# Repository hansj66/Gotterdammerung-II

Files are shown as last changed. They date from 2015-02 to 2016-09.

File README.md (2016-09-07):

# Götterdämmerung II 3D-printer

GD2

This is the second iteration of the Götterdämmerung. The following improvements have been made:
- Core XY'ish layout. 
- Dual 24V power. 
- Improved Z stage.
- Geared stepper extruder, using M2 type filament drive.
- Designed for using cable towing chains.

Suggestions for selecting necessary third party stuff for building a complete printer

- Use 24 V power. This will enable you to run the steppers faster and use thinner wires. Also use a separate power supply for the heated bed (driven via a solid state relay)
- Buy a decent hot end. E3D with a 0.8 mm nozzle (or bigger) works fine with this printer.
- Use glass fiber reinforced timing belts.
- Use low impedance steppers.

Rumba board (supports 24V) with DRV8825, configured for 1/16 microstepping works fine with this printer. 

This is a working design, but it is still in development. 

The printer frame is made of 40x40 mm aluminium extrusions and it is extremely rigid. All idlers use ball bearings and 
the combination of 12mm steel axis and linear bearings ensures a stable platform.
The design scales in X/Y/Z without changes to any printed parts.

Build instructions (work in progress)  can be found on the wiki pages: https://github.com/hansj66/Gotterdammerung-II/wiki

Other stuff that has been printed on this printer:

Model from Bold machines. Scaled to approximately 25x20x14 cm in size.
Margo's Dog

Dante bust (29 x 30 x 26 cm). 13 hours print with 0.8mm nozzle, 0.3mm layer height

Dante

Strandbeest inspired robots. Theo Jansen linkage, but with parameters based on output from my own genetic algorithm). 80+ hours printing time.

City Beest

CityBeest mk II

This design is made available under the under the Creative Commons Attribution-ShareAlike CC BY-NC-SA license (https://creativecommons.org/licenses/by-nc-sa/4.0/)



Hans Jørgen Grimstad
www.TimeExpander.com

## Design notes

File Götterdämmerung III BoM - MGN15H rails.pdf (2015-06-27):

Item # | Count | Dimension | Description
1 | 9 | (m) 40x40 | aluminium profile
2 | 24 | 40 x 40 | aluminium angle brackets
3 | 50 | M8 | T-nuts
4 | 40 | M8 | 15 mm hex head bolt
5 | 10 | M8 | 25 mm hex head bolt
6 | 2 | | 24V Power Supply (360W+ for heatbed PS)
7 | 1 | | Rumba board
8 | 4 | | DRV8825 + heatsinks
9 | 1 | | Ramps 1.4 smart controller (Display, SD, Encoder)
10 | 1 | | Geared Nema 17
11 | 3 | | Nema 17 1,8 A
12 | 4 | 500 mm | 8mm Lead Screw with nut
13 | 2 | 500 mm | 12 MM Steel rods
14 | 2 | 500 mm | MGN15H Linear rails (25x25mm M3 hole separation on carriage)
15 | 1 | 600 mm | MGN15H Linear rails (25x25mm M3 hole separation on carriage)
16 | 16 | OD: 22 ID 8 H 7 | Ball bearings
17 | 20 | M8 | washer
18 | 4 | M8 | hex nut
19 | 14 | ID: 8: OD 30 | M8 washer
20 | 4 | ID: 8 mm | GT2 pulleys
21 | 3 | ID: 5 mm | GT2 pulleys
22 | 2 | LM12UU | Linear bearings
23 | 4 | m | Open GT2 belt
24 | 1 | 1524 mm | Closed GT2 belt
25 | 1 | 5x8 | Flexible shaft coupling
26 | 2 | 500 mm (10 x 1 | CNC Cable Carrier Drag Chain
27 | 1 | E3D HotEnd | (Or other J-head equivalent)
28 | 1 | 8 x 25 mm spring
29 | 2 | 200x300 | Heatbed
30 | 2 | 200x300 | Cork insulation

31 | 1 | 100k ? | Thermistor for heatbed
32 | 2 | 68x145x200mm | Enclosure
33 | 1 | Ø 25 mm | Rod for spool holder
34 | 20 | (m) | Wiring. Different colours
35 | 3 | | End stops + cables
36 | 20 | 5mm | M3 screws
37 | 50 | 20 mm | M3 screws
38 | 1 | m | 6mm carbon tube/rod
39 | 1 | | Solid State DC Relay (SSR-25DD or equivalent)
40 | 1 | | Build plate, MDF (16 x 400 x 440 mm)
41 | 1 | | Aluminium sheet, 1 x 400 x 440 mm)
42 | 1 | | Glass plate ( 3 x 400 x 440 mm)
43 | | | Printed parts
44 | 1 | | http://www.thingiverse.com/thing:494430

Subject to change as improvements are made

All non-printed parts for the initial version were sourced from eBay or AliExpress for approx $1100

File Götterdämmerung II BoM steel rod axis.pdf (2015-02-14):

Item # | Count | Dimension | Description
1 | 9 | (m) 40x40 | aluminium profile
2 | 24 | 40 x 40 | aluminium angle brackets
3 | 50 | M8 | T-nuts
4 | 40 | M8 | 15 mm hex head bolt
5 | 10 | M8 | 25 mm hex head bolt
6 | 2 | | 24V Power Supply (360W+ for heatbed PS)
7 | 1 | | Rumba board
8 | 4 | | DRV8825 + heatsinks
9 | 1 | | Ramps 1.4 smart controller (Display, SD, Encoder)
10 | 1 | | Geared Nema 17
11 | 3 | | Nema 17 1,8 A
12 | 2 | (m) | M8 Z screw
13 | 6 | 500 mm | 12 MM Steel rods
14 | 16 | OD: 22 ID 8 H 7 | Ball bearings
15 | 20 | M8 | washer
16 | 4 | M8 | hex nut
17 | 14 | ID: 8: OD 30 | M8 washer
18 | 4 | ID: 8 mm | GT2 pulleys
19 | 3 | ID: 5 mm | GT2 pulleys
20 | 6 | LM12UU | Linear bearings
21 | 4 | m | Open GT2 belt
22 | 1 | 1524 mm | Closed GT2 belt
23 | 1 | 5x8 | Flexible shaft coupling
24 | 2 | 500 mm (10 x 1 | CNC Cable Carrier Drag Chain
25 | 1 | E3D HotEnd | (Or other J-head equivalent)
26 | 1 | 8 x 25 mm spring
27 | 2 | 200x300 | Heatbed
28 | 2 | 200x300 | Cork insulation
29 | 1 | 100k ? | Thermistor for heatbed
30 | 2 | 68x145x200mm | Enclosure

31 | 1 | Ø 25 mm | Rod for spool holder
32 | 20 | (m) | Wiring. Different colours
33 | 3 | | End stops + cables
34 | 20 | 5mm | M3 screws
35 | 50 | 20 mm | M3 screws
36 | 1 | m | 6mm carbon tube/rod
37 | 1 | | Solid State DC Relay (SSR-25DD or equivalent)
38 | 1 | | Build plate, MDF (16 x 400 x 440 mm)
39 | 1 | | Aluminium sheet, 1 x 400 x 440 mm)
40 | 1 | | Glass plate ( 3 x 400 x 440 mm)
41 | | | Printed parts
42 | 1 | | http://www.thingiverse.com/thing:494430

Subject to change as improvements are made

All non-printed parts for the initial version were sourced from eBay or AliExpress for approx $1000

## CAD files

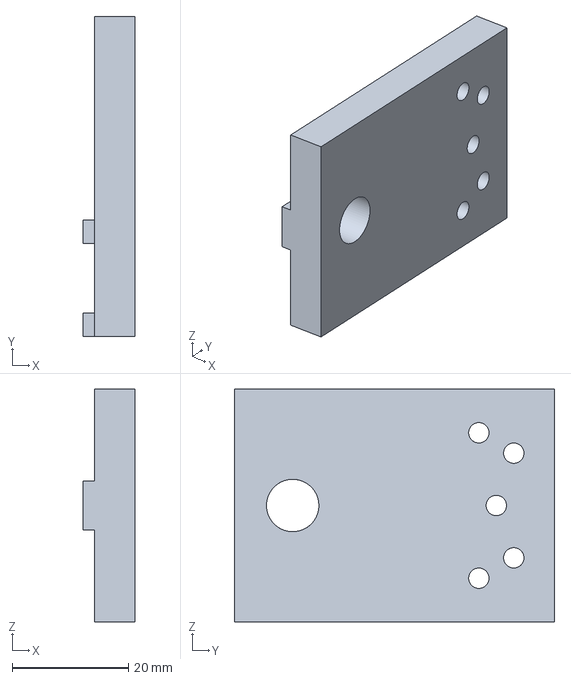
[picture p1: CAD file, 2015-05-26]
printed_parts/beta/IGES/Generic_Power_Mount_Small.igs
9.00 x 55.0 x 40.0 mm

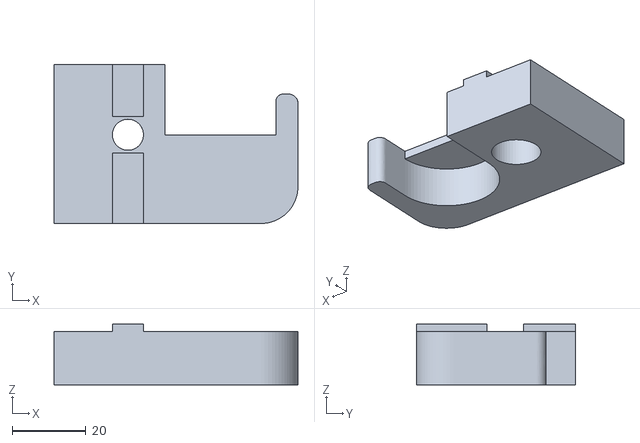
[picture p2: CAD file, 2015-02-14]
printed_parts/beta/STL/FilamentRodHolder_L.stl
66.0 x 43.0 x 16.5

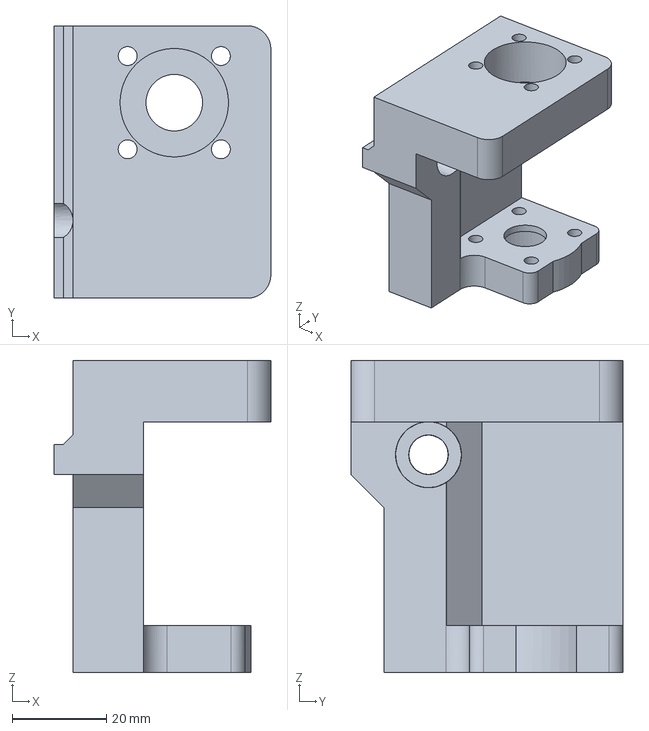
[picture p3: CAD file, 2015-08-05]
printed_parts/production/IGES/z-stepper-mount-geared.igs
46.0 x 57.8 x 66.2 mm

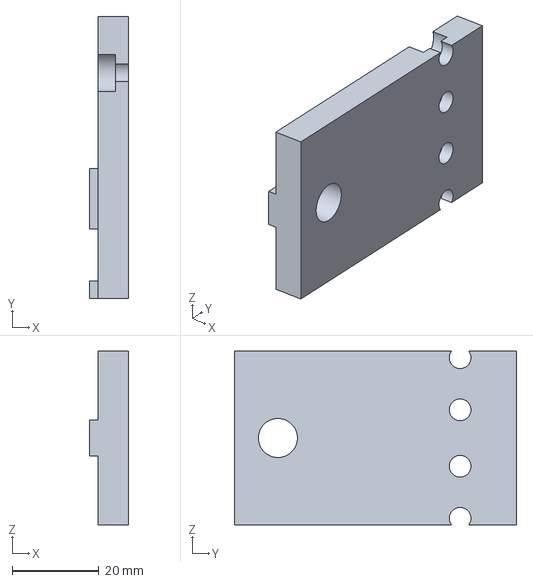
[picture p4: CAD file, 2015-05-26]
printed_parts/beta/IGES/Generic_Power_Mount_Big.igs
9.00 x 65.0 x 40.0 mm

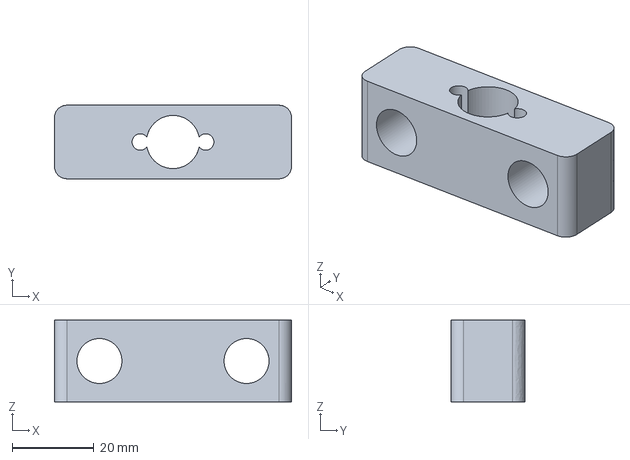
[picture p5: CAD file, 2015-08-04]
printed_parts/production/IGES/z-adjustment-T8.igs
58.0 x 18.0 x 20.0 mm

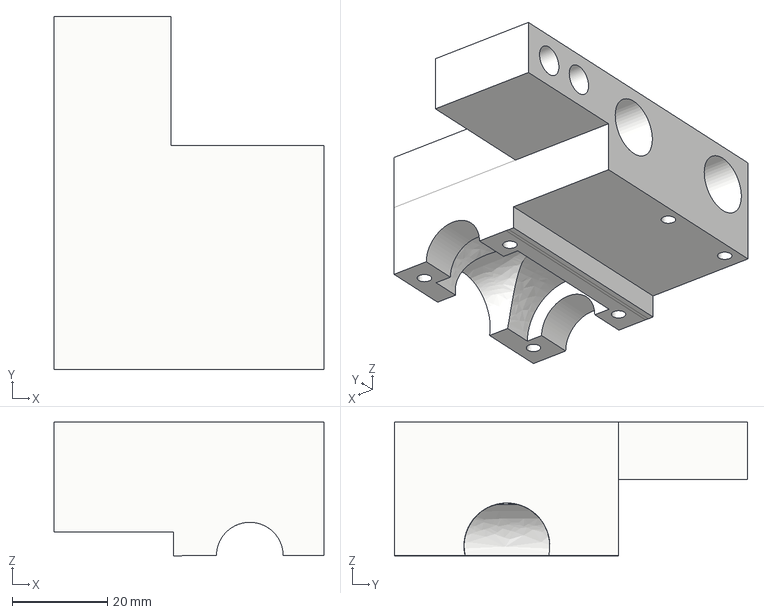
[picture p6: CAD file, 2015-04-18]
printed_parts/beta/IGES/Y_Carriage_Left_2.igs
56.5 x 74.0 x 28.0 mm

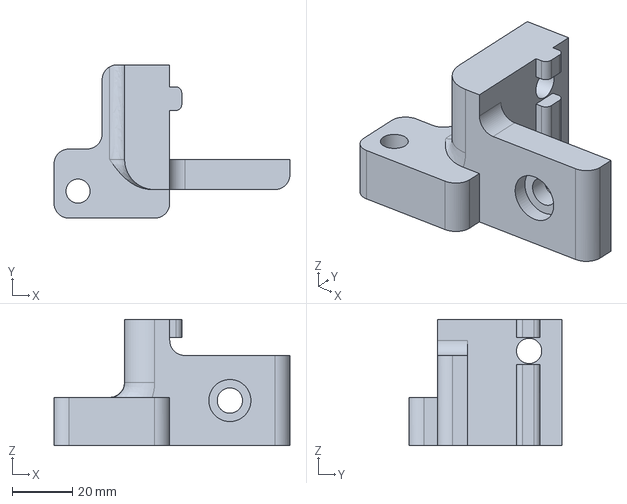
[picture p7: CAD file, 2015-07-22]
printed_parts/production/IGES/XY_Idler_Left.igs
78.5 x 51.0 x 42.0 mm

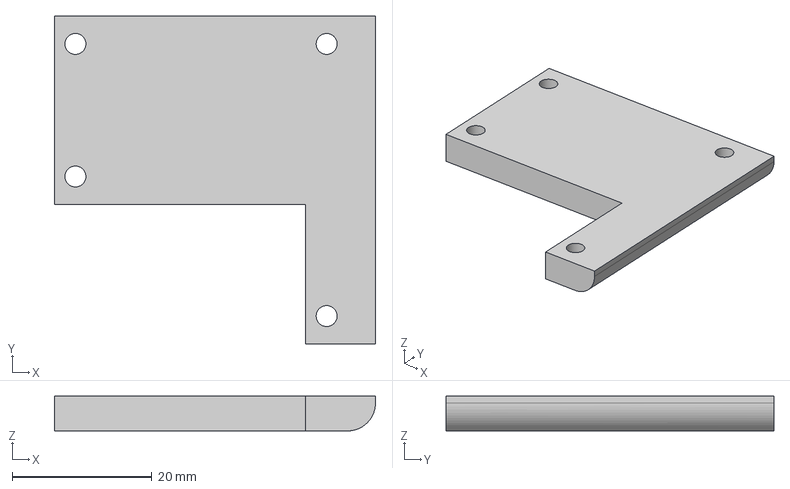
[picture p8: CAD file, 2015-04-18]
printed_parts/beta/IGES/Y_Carriage_Right_4.igs
46.0 x 47.0 x 5.00 mm

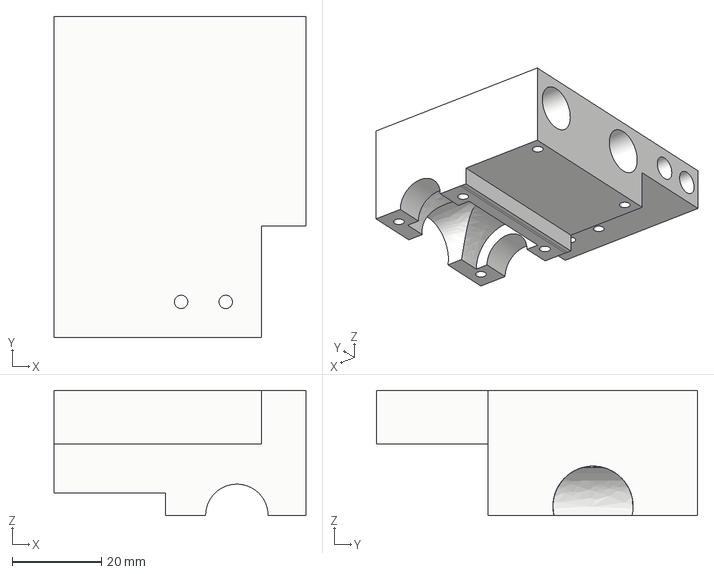
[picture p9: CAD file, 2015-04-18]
printed_parts/beta/IGES/Y_Carriage_Right_2.igs
56.5 x 72.0 x 28.0 mm

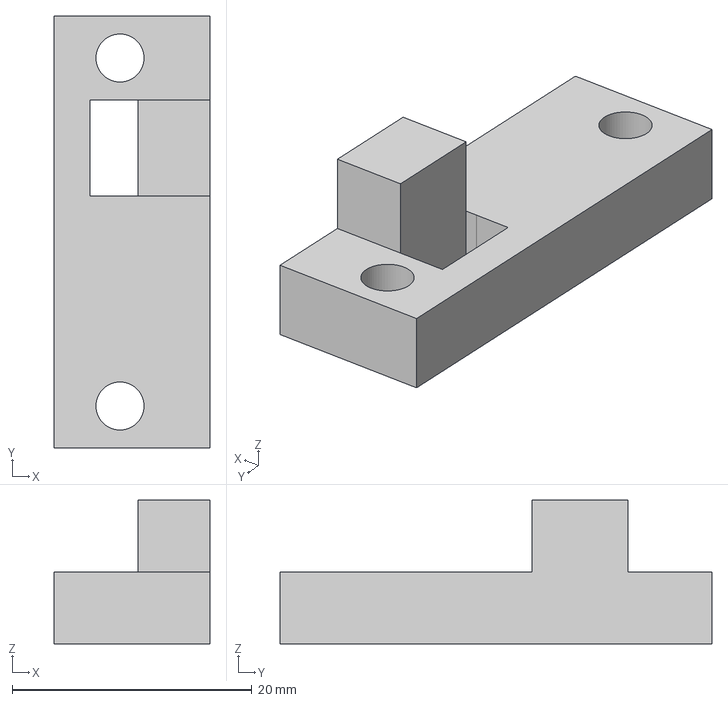
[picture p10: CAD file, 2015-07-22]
printed_parts/production/IGES/Clamp1.igs
13.0 x 36.0 x 12.0 mm

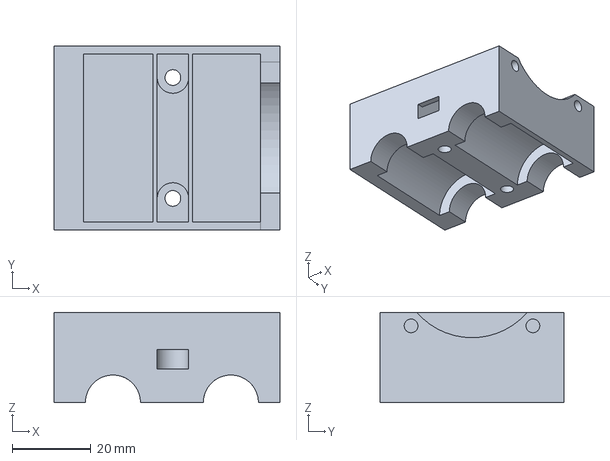
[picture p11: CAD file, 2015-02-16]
printed_parts/beta/IGES/X_Carriage_7.igs
57.5 x 46.8 x 22.9 mm

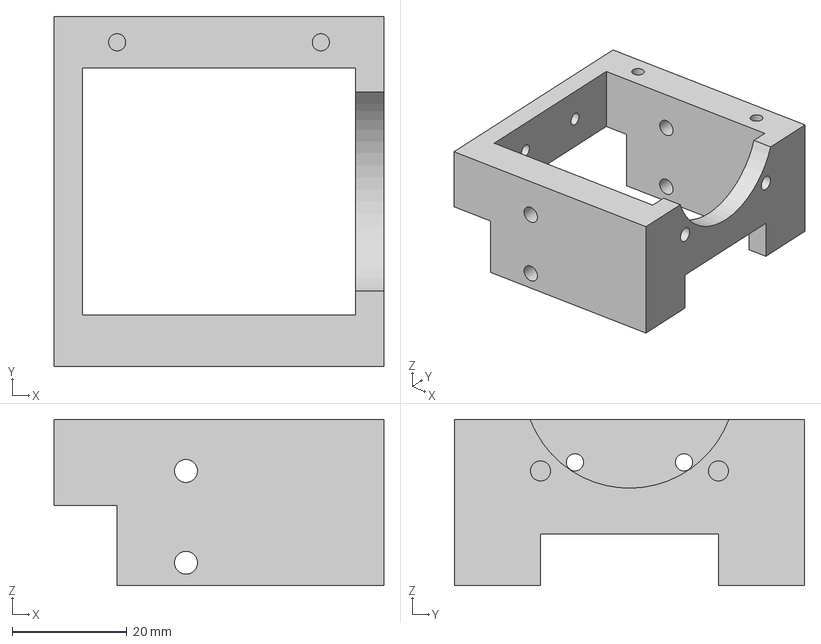
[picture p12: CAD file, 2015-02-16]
printed_parts/beta/IGES/X_Carriage_2.igs
57.5 x 61.0 x 29.0 mm

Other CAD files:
printed_parts/production/STL/FilamentRodHolder_R.stl
printed_parts/beta/STL/FilamentRodHolder_R.stl
printed_parts/production/IGES/XY_Idler_Right.igs
printed_parts/production/IGES/Clamp3.igs
printed_parts/production/IGES/Clamp2.igs
printed_parts/beta/IGES/ATX_Power_Mount_1.igs
printed_parts/beta/IGES/ATX_Power_Mount_2.igs
printed_parts/beta/IGES/ATX_Power_Mount_3.igs
printed_parts/beta/IGES/Cable_Clamp.igs
printed_parts/beta/IGES/Display_Enclosure_1.igs
printed_parts/beta/IGES/Display_Enclosure_2.igs
printed_parts/beta/IGES/Display_Enclosure_3.igs
printed_parts/beta/IGES/FilamentRodHolder_Make_Mirror_Copy.igs
printed_parts/beta/IGES/XY_Idler_Left_1.igs
printed_parts/beta/IGES/XY_Idler_Left_2.igs
printed_parts/beta/IGES/XY_Idler_Right.igs
printed_parts/beta/IGES/XY_Stepper_Mount_Left.igs
printed_parts/beta/IGES/XY_Stepper_Mount_Right.igs
printed_parts/beta/IGES/X_Carriage_1.igs
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

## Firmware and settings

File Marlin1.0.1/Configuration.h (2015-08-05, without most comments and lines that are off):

#define CONFIGURATION_H
#include "boards.h"
#define STRING_VERSION_CONFIG_H __DATE__ " " __TIME__ // build date and time
#define STRING_CONFIG_H_AUTHOR "(none, default config)" // Who made the changes.
#define SERIAL_PORT 0
#define BAUDRATE 250000
  #define MOTHERBOARD BOARD_RUMBA
#define CUSTOM_MENDEL_NAME "GD "
#define EXTRUDERS 1
#define POWER_SUPPLY 1
#define TEMP_SENSOR_0 5
#define TEMP_SENSOR_1 0
#define TEMP_SENSOR_2 0
#define TEMP_SENSOR_BED 4
#define MAX_REDUNDANT_TEMP_SENSOR_DIFF 10
#define TEMP_RESIDENCY_TIME 10  // (seconds)
#define TEMP_HYSTERESIS 3       // (degC) range of +/- temperatures considered "close" to the target one
#define TEMP_WINDOW     1       // (degC) Window around target to start the residency timer x degC early.
#define HEATER_0_MINTEMP 5
#define HEATER_1_MINTEMP 5
#define HEATER_2_MINTEMP 5
#define BED_MINTEMP 5
#define HEATER_0_MAXTEMP 275
#define HEATER_1_MAXTEMP 275
#define HEATER_2_MAXTEMP 275
#define BED_MAXTEMP 60
#define PIDTEMP
#define BANG_MAX 200 // limits current to nozzle while in bang-bang mode; 255=full current
#define PID_MAX BANG_MAX // limits current to nozzle while PID is active (see PID_FUNCTIONAL_RANGE below); 255=full current
  #define PID_FUNCTIONAL_RANGE 10 // If the temperature difference between the target temperature and the actual temperature
  #define PID_INTEGRAL_DRIVE_MAX PID_MAX  //limit for the integral term
  #define K1 0.95 //smoothing factor within the PID
  #define PID_dT ((OVERSAMPLENR * 10.0)/(F_CPU / 64.0 / 256.0)) //sampling period of the temperature routine
    #define  DEFAULT_Kp 22.2
    #define  DEFAULT_Ki 1.08
    #define  DEFAULT_Kd 114
#define MAX_BED_POWER 128 // limits duty cycle to bed; 255=full current
#define PREVENT_DANGEROUS_EXTRUDE
#define PREVENT_LENGTHY_EXTRUDE
#define EXTRUDE_MINTEMP 170
#define EXTRUDE_MAXLENGTH (X_MAX_LENGTH+Y_MAX_LENGTH) //prevent extrusion of very large distances.
#define COREXY
#define ENDSTOPPULLUPS // Comment this out (using // at the start of the line) to disable the endstop pullup resistors
  #define ENDSTOPPULLUP_XMAX
  #define ENDSTOPPULLUP_YMAX
  #define ENDSTOPPULLUP_ZMAX
  #define ENDSTOPPULLUP_XMIN
  #define ENDSTOPPULLUP_YMIN
  #define ENDSTOPPULLUP_ZMIN
const bool X_MIN_ENDSTOP_INVERTING = true; // set to true to invert the logic of the endstop.
const bool Y_MIN_ENDSTOP_INVERTING = true; // set to true to invert the logic of the endstop.
const bool Z_MIN_ENDSTOP_INVERTING = true; // set to true to invert the logic of the endstop.
const bool X_MAX_ENDSTOP_INVERTING = true; // set to true to invert the logic of the endstop.
const bool Y_MAX_ENDSTOP_INVERTING = true; // set to true to invert the logic of the endstop.
const bool Z_MAX_ENDSTOP_INVERTING = true; // set to true to invert the logic of the endstop.
#if defined(COREXY) && !defined(DISABLE_MAX_ENDSTOPS)
  #define DISABLE_MAX_ENDSTOPS
#endif
#define X_ENABLE_ON 0
#define Y_ENABLE_ON 0
#define Z_ENABLE_ON 0
#define E_ENABLE_ON 0 // For all extruders
#define DISABLE_X false
#define DISABLE_Y false
#define DISABLE_Z false
#define DISABLE_E false // For all extruders
#define DISABLE_INACTIVE_EXTRUDER true //disable only inactive extruders and keep active extruder enabled
#define INVERT_X_DIR true    // for Mendel set to false, for Orca set to true
#define INVERT_Y_DIR false    // for Mendel set to true, for Orca set to false
#define INVERT_Z_DIR false     // for Mendel set to false, for Orca set to true
#define INVERT_E0_DIR false   // for direct drive extruder v9 set to true, for geared extruder set to false
#define INVERT_E1_DIR false    // for direct drive extruder v9 set to true, for geared extruder set to false
#define INVERT_E2_DIR false   // for direct drive extruder v9 set to true, for geared extruder set to false
#define X_HOME_DIR -1
#define Y_HOME_DIR -1
#define Z_HOME_DIR -1
#define min_software_endstops true // If true, axis won't move to coordinates less than HOME_POS.
#define max_software_endstops true  // If true, axis won't move to coordinates greater than the defined lengths below.
#define X_MAX_POS 340
#define X_MIN_POS 0
#define Y_MAX_POS 340
#define Y_MIN_POS 0
#define Z_MAX_POS 200
#define Z_MIN_POS 0
#define X_MAX_LENGTH (X_MAX_POS - X_MIN_POS)
#define Y_MAX_LENGTH (Y_MAX_POS - Y_MIN_POS)
#define Z_MAX_LENGTH (Z_MAX_POS - Z_MIN_POS)
#define Z_PROBE_REPEATABILITY_TEST  // If not commented out, Z-Probe Repeatability test will be included if Auto Bed Leveling is Enabled.
#define MANUAL_X_HOME_POS 0
#define MANUAL_Y_HOME_POS 0
#define MANUAL_Z_HOME_POS 0
#define NUM_AXIS 4 // The axis order in all axis related arrays is X, Y, Z, E
#define HOMING_FEEDRATE {50*60, 50*60, 4*60, 0}  // set the homing speeds (mm/min)
#define DEFAULT_AXIS_STEPS_PER_UNIT   {160,160,518,475}  // M8 leadscrew. geared stepper 1/8 microstepping. 17HS15-1684S-PG5
#define DEFAULT_MAX_FEEDRATE          {150, 150, 2, 150}    // (mm/sec)
#define DEFAULT_MAX_ACCELERATION      {9000,9000,50,10000}    // X, Y, Z, E maximum start speed for accelerated moves. E default values are good for Skeinforge 40+, for older versions raise them a lot.
#define DEFAULT_ACCELERATION          900    // X, Y, Z and E max acceleration in mm/s^2 for printing moves
#define DEFAULT_RETRACT_ACCELERATION  1500   // X, Y, Z and E max acceleration in mm/s^2 for retracts
#define DEFAULT_XYJERK                10.0    // (mm/sec)
#define DEFAULT_ZJERK                 0.4     // (mm/sec)
#define DEFAULT_EJERK                 5.0    // (mm/sec)
#define CUSTOM_M_CODES
  #define CUSTOM_M_CODE_SET_Z_PROBE_OFFSET 851
  #define Z_PROBE_OFFSET_RANGE_MIN -15
  #define Z_PROBE_OFFSET_RANGE_MAX -5
#define PLA_PREHEAT_HOTEND_TEMP 220
#define PLA_PREHEAT_HPB_TEMP 50
#define PLA_PREHEAT_FAN_SPEED 255   // Insert Value between 0 and 255
#define ABS_PREHEAT_HOTEND_TEMP 240
#define ABS_PREHEAT_HPB_TEMP 100
#define ABS_PREHEAT_FAN_SPEED 255   // Insert Value between 0 and 255
#define REPRAP_DISCOUNT_FULL_GRAPHIC_SMART_CONTROLLER
 #define DOGLCD
 #define U8GLIB_ST7920
 #define REPRAP_DISCOUNT_SMART_CONTROLLER
 #define ULTIPANEL
 #define NEWPANEL
  #define SDSUPPORT
  #define ULTRA_LCD
    #define LCD_WIDTH 20
    #define LCD_HEIGHT 5
#  define DEFAULT_LCD_CONTRAST 32
#define SOFT_PWM_SCALE 0
#define FILAMENT_SENSOR_EXTRUDER_NUM	0  //The number of the extruder that has the filament sensor (0,1,2)
#define MEASUREMENT_DELAY_CM			14  //measurement delay in cm.  This is the distance from filament sensor to middle of barrel
#define DEFAULT_NOMINAL_FILAMENT_DIA  3.0  //Enter the diameter (in mm) of the filament generally used (3.0 mm or 1.75 mm) - this is then used in the slicer software.  Used for sensor reading validation
#define MEASURED_UPPER_LIMIT          3.30  //upper limit factor used for sensor reading validation in mm
#define MEASURED_LOWER_LIMIT          1.90  //lower limit factor for sensor reading validation in mm
#define MAX_MEASUREMENT_DELAY			20  //delay buffer size in bytes (1 byte = 1cm)- limits maximum measurement delay allowable (must be larger than MEASUREMENT_DELAY_CM  and lower number saves RAM)
#define DEFAULT_MEASURED_FILAMENT_DIA  DEFAULT_NOMINAL_FILAMENT_DIA  //set measured to nominal initially
#include "Configuration_adv.h"
#include "thermistortables.h"

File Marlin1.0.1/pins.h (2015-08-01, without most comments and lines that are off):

#define PINS_H
#include "boards.h"
#if !MB(5DPRINT)
#define X_MS1_PIN -1
#define X_MS2_PIN -1
#define Y_MS1_PIN -1
#define Y_MS2_PIN -1
#define Z_MS1_PIN -1
#define Z_MS2_PIN -1
#define E0_MS1_PIN -1
#define E0_MS2_PIN -1
#define E1_MS1_PIN -1
#define E1_MS2_PIN -1
#define DIGIPOTSS_PIN -1
#endif
#if MB(5DPRINT)
#define KNOWN_BOARD 1
#define AT90USB 1286  // Disable MarlinSerial etc.
#ifndef __AVR_AT90USB1286__
#error Oops!  Make sure you have 'Teensy++ 2.0' selected from the 'Tools -> Boards' menu.
#endif
#define LARGE_FLASH        true
#define X_STEP_PIN          0
#define X_DIR_PIN           1
#define X_ENABLE_PIN       23
#define X_STOP_PIN         37
#define Y_STEP_PIN          2
#define Y_DIR_PIN           3
#define Y_ENABLE_PIN       19
#define Y_STOP_PIN         36
#define Z_STEP_PIN          4
#define Z_DIR_PIN           5
#define Z_ENABLE_PIN       18
#define Z_STOP_PIN         39
#define E0_STEP_PIN         6
#define E0_DIR_PIN          7
#define E0_ENABLE_PIN      17
#define HEATER_0_PIN       21  // Extruder
#define HEATER_1_PIN       -1
#define HEATER_2_PIN       -1
#define HEATER_BED_PIN     20  // Bed
#define FAN_PIN            16  // Fan
#define TEMP_0_PIN          1  // Extruder / Analog pin numbering
#define TEMP_BED_PIN        0  // Bed / Analog pin numbering
#define TEMP_1_PIN         -1
#define TEMP_2_PIN         -1
#define SDPOWER            -1
#define LED_PIN            -1
#define PS_ON_PIN          -1
#define KILL_PIN           -1
#define ALARM_PIN          -1
#define SDSS               20
#define X_MS1_PIN 25
#define X_MS2_PIN 26
#define Y_MS1_PIN 9
#define Y_MS2_PIN 8
#define Z_MS1_PIN 7
#define Z_MS2_PIN 6
#define E0_MS1_PIN 5
#define E0_MS2_PIN 4
#endif // 5DPRINT
#if MB(LEAPFROG)  // Leapfrog board
#define KNOWN_BOARD 1
#ifndef __AVR_ATmega1280__
 #ifndef __AVR_ATmega2560__
 #error Oops!  Make sure you have 'Arduino Mega' selected from the 'Tools -> Boards' menu.
 #endif
#endif
#define X_STEP_PIN         28
#define X_DIR_PIN          63
#define X_ENABLE_PIN       29
#define X_MIN_PIN          47
#define X_MAX_PIN          -1   //2 //Max endstops default to disabled "-1", set to commented value to enable.
#define Y_STEP_PIN         14 // A6
#define Y_DIR_PIN          15 // A0
#define Y_ENABLE_PIN       39
#define Y_MIN_PIN          48
#define Y_MAX_PIN          -1   //15
#define Z_STEP_PIN         31 // A2
#define Z_DIR_PIN          32 // A6
#define Z_ENABLE_PIN       30 // A1
#define Z_MIN_PIN          49
#define Z_MAX_PIN          -1
#define E0_STEP_PIN         34  //34
#define E0_DIR_PIN          35 //35
#define E0_ENABLE_PIN       33 //33
#define E1_STEP_PIN         37 //37
#define E1_DIR_PIN          40 //40
#define E1_ENABLE_PIN       36 //36
#define Y2_STEP_PIN         37
#define Y2_DIR_PIN          40
#define Y2_ENABLE_PIN       36
#define Z2_STEP_PIN         37
#define Z2_DIR_PIN          40
#define Z2_ENABLE_PIN       36
#define SDPOWER            -1
#define SDSS               11
#define SDCARDDETECT       -1 // 10 optional also used as mode pin
#define LED_PIN            13
#define FAN_PIN            7
#define PS_ON_PIN          -1
#define KILL_PIN           -1
#define SOL1_PIN   16
#define SOL2_PIN    17
#define HEATER_0_PIN       9
#define HEATER_1_PIN       8 // 12
#define HEATER_2_PIN       11 //-1 // 13
#define TEMP_0_PIN         13 //D27   // MUST USE ANALOG INPUT NUMBERING NOT DIGITAL OUTPUT NUMBERING!!!!!!!!!
#define TEMP_1_PIN         15 // 1
#define TEMP_2_PIN         -1 // 2
#define HEATER_BED_PIN     10 // 14/15
#define TEMP_BED_PIN       14 // 1,2 or I2C
#endif // LEAPFROG
#if MB(99)
#define KNOWN_BOARD 1
#define X_STEP_PIN          2
#define X_DIR_PIN           3
#define X_ENABLE_PIN        -1
#define X_STOP_PIN          16
#define Y_STEP_PIN          5
#define Y_DIR_PIN           6
#define Y_ENABLE_PIN       -1
#define Y_STOP_PIN          67
#define Z_STEP_PIN          62
#define Z_DIR_PIN           63
#define Z_ENABLE_PIN       -1
#define Z_STOP_PIN          59
#define E0_STEP_PIN         65
#define E0_DIR_PIN          66
#define E0_ENABLE_PIN      -1
#define SDPOWER            -1
#define SDSS               53
#define LED_PIN            -1
#define FAN_PIN            -1
#define PS_ON_PIN           9
#define KILL_PIN           -1
#define HEATER_0_PIN        13
#define HEATER_1_PIN       -1
#define HEATER_2_PIN       -1
#define TEMP_0_PIN          6   // MUST USE ANALOG INPUT NUMBERING NOT DIGITAL OUTPUT NUMBERING!!!!!!!!!
#define TEMP_1_PIN         -1   // MUST USE ANALOG INPUT NUMBERING NOT DIGITAL OUTPUT NUMBERING!!!!!!!!!
#define TEMP_2_PIN         -1   // MUST USE ANALOG INPUT NUMBERING NOT DIGITAL OUTPUT NUMBERING!!!!!!!!!
#define HEATER_BED_PIN      4
#define TEMP_BED_PIN       10
#endif // 99
#if MB(SETHI)
#define KNOWN_BOARD
#if !defined(__AVR_ATmega644P__) && !defined(__AVR_ATmega644__) && !defined(__AVR_ATmega1284P__)
#error Oops! Make sure you have 'Sethi 3D' selected from the 'Tools -> Boards' menu.
#endif
#define GEN7_VERSION 12 // v1.x
#define X_STEP_PIN 19
#define X_DIR_PIN 18
#define X_ENABLE_PIN 24
#define X_STOP_PIN 2
#define Y_STEP_PIN 23
#define Y_DIR_PIN 22
#define Y_ENABLE_PIN 24
#define Y_STOP_PIN 0
#define Z_STEP_PIN 26
#define Z_DIR_PIN 25
#define Z_ENABLE_PIN 24
#define Z_MIN_PIN 1
#define Z_MAX_PIN 0
#define E0_STEP_PIN 28
#define E0_DIR_PIN 27
#define E0_ENABLE_PIN 24
#define TEMP_0_PIN 1
#define TEMP_1_PIN -1
#define TEMP_2_PIN -1
#define TEMP_BED_PIN 2
#define HEATER_0_PIN 4
#define HEATER_1_PIN -1
#define HEATER_2_PIN -1
#define HEATER_BED_PIN 3
#define KILL_PIN -1
#define SDPOWER -1
#define SDSS -1 // SCL pin of I2C header
#define LED_PIN -1
#if (GEN7_VERSION >= 13)
#define FAN_PIN -1
#else
#define FAN_PIN 31
#endif
#define PS_ON_PIN 15
#define BOGUS_TEMPERATURE_FAILSAFE_OVERRIDE
#define DEBUG_PIN 0
#define TX_ENABLE_PIN 12
#define RX_ENABLE_PIN 13
#endif // SETHI
#if MB(GEN7_13)
#define MOTHERBOARD BOARD_GEN7_12
#define GEN7_VERSION 13 // v1.3
#endif
#if MB(GEN7_12)
#define KNOWN_BOARD
#if !defined(__AVR_ATmega644P__) && !defined(__AVR_ATmega644__) && !defined(__AVR_ATmega1284P__)
#error Oops! Make sure you have 'Gen7' selected from the 'Tools -> Boards' menu.
#endif
#ifndef GEN7_VERSION
#define GEN7_VERSION 12 // v1.x
#endif
#define X_STEP_PIN 19
#define X_DIR_PIN 18
#define X_ENABLE_PIN 24
#define X_STOP_PIN 7
#define Y_STEP_PIN 23
#define Y_DIR_PIN 22
#define Y_ENABLE_PIN 24
#define Y_STOP_PIN 5
#define Z_STEP_PIN 26
#define Z_DIR_PIN 25
#define Z_ENABLE_PIN 24
#define Z_MIN_PIN 1
#define Z_MAX_PIN 0
#define E0_STEP_PIN 28
#define E0_DIR_PIN 27
#define E0_ENABLE_PIN 24
#define TEMP_0_PIN 1
#define TEMP_1_PIN -1
#define TEMP_2_PIN -1
#define TEMP_BED_PIN 2
#define HEATER_0_PIN 4
#define HEATER_1_PIN -1
#define HEATER_2_PIN -1
#define HEATER_BED_PIN 3
#define KILL_PIN -1
#define SDPOWER -1
#define SDSS -1 // SCL pin of I2C header
#define LED_PIN -1
#if (GEN7_VERSION >= 13)
#define FAN_PIN -1
#else
#define FAN_PIN 31
#endif
#define PS_ON_PIN 15
#define BOGUS_TEMPERATURE_FAILSAFE_OVERRIDE
#define DEBUG_PIN 0
#define TX_ENABLE_PIN 12
#define RX_ENABLE_PIN 13
#endif
#if MB(GEN7_14)
#define GEN7_VERSION 14 // v1.4
#endif
#if MB(GEN7_14)
#define KNOWN_BOARD
#if !defined(__AVR_ATmega644P__) && !defined(__AVR_ATmega644__) && !defined(__AVR_ATmega1284P__)
#error Oops! Make sure you have 'Gen7' selected from the 'Tools -> Boards' menu.
#endif
#ifndef GEN7_VERSION
#define GEN7_VERSION 14 // v1.x
#endif
#define X_STEP_PIN 29
#define X_DIR_PIN 28
#define X_ENABLE_PIN 25
#define X_STOP_PIN 0
#define Y_STEP_PIN 27
#define Y_DIR_PIN 26
#define Y_ENABLE_PIN 25
#define Y_STOP_PIN 1
#define Z_STEP_PIN 23
#define Z_DIR_PIN 22
#define Z_ENABLE_PIN 25
#define Z_STOP_PIN 2
#define E0_STEP_PIN 19
#define E0_DIR_PIN 18
#define E0_ENABLE_PIN 25
#define TEMP_0_PIN 1
#define TEMP_1_PIN -1
#define TEMP_2_PIN -1
#define TEMP_BED_PIN 0
#define HEATER_0_PIN 4
#define HEATER_1_PIN -1
#define HEATER_2_PIN -1
#define HEATER_BED_PIN 3
#define KILL_PIN -1
#define SDPOWER -1
#define SDSS -1 // SCL pin of I2C header
#define LED_PIN -1
#define FAN_PIN -1
#define PS_ON_PIN 15
#define DEBUG_PIN 0
#define TX_ENABLE_PIN 12
#define RX_ENABLE_PIN 13
#endif // GEN7
#if MB(GEN7_CUSTOM)
#define KNOWN_BOARD
#if !defined(__AVR_ATmega644P__) && !defined(__AVR_ATmega644__) && !defined(__AVR_ATmega1284P__)
    #error Oops!  Make sure you have 'Gen7' selected from the 'Tools -> Boards' menu.
#endif
    #define X_STEP_PIN      21                  // different from standard GEN7
    #define X_DIR_PIN       20                  // different from standard GEN7
    #define X_ENABLE_PIN    24
    #define X_STOP_PIN      0
    #define Y_STEP_PIN      23
    #define Y_DIR_PIN       22
    #define Y_ENABLE_PIN    24
    #define Y_STOP_PIN      1
    #define Z_STEP_PIN      26
    #define Z_DIR_PIN       25
    #define Z_ENABLE_PIN    24
    #define Z_STOP_PIN      2
    #define E0_STEP_PIN      28
    #define E0_DIR_PIN       27
    #define E0_ENABLE_PIN    24
    #define TEMP_0_PIN      2
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

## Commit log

2015-02-16 Removed artefact (used for aligning bodies)
    [X_Carriage_2.igs, X_Carriage_2.stl, X_Carriage_7.igs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]
2015-02-20 Added a few pictures of test prints
2015-04-18 Added profile for Alloy 910. Minor modifications to carriage.
    [ATX_Power_Mount_1.stl, ATX_Power_Mount_2.stl, ATX_Power_Mount_3.stl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]
2015-04-18 Lost some dead plastic
    [Y_Carriage_Left_2.igs, Y_Carriage_Left_2.stl]
2015-05-26 Preparing for linear rails
    Also updated configuration with number of steps for Z .
    [ATX_Power_Mount_1.igs, ATX_Power_Mount_1.stl, ATX_Power_Mount_2.igs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]
2015-05-30 Added Y-Carriage and belt idler for linear MGN15H rails
    [Y-Carriage.igs, Y-Carriage.stl, Y-Idler1.igs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]
2015-05-31 Added two new components
    Towing chain support for X-rail and nylon washer
    [Nylon_Washer.igs, Nylon_Washer.stl, X-Towing-Chain-Support.igs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]
2015-05-31 Added new components
    Renamed Nylon_Washer to Washer1.
    Added two other washers
    Added XY Idler (left)
    Imported E3D mounting bracket (from Thingiverse)
    [E3D_v6_New_Extruder.stp, Spacer1.igs, Spacer1.stl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]
2015-06-02 Minor adjustements
    a) Adjusted of hole sizes
    b) Made XY_Idler_Right into a pure mirror of the left version
    [Spacer1.igs, Spacer1.stl, Washer2.igs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]
2015-06-02 Adjusted length of spacer for X/Y idlers
    [Spacer1.igs, Spacer1.stl]
2015-06-02 Added Relay Bracket
    Fits SSR-25 DD (And probably most other types)
    [Relay_Bracket.igs, Relay_Bracket.stl]
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2015-06-04 XY_Carriage and belt clamps for rail
    [Clamp1.igs, Clamp1.stl, Clamp2.igs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]
2015-06-04 Updated clamp4 to double as X endstop
    also increased size of stepper mounting hole
    [Clamp4.igs, Clamp4.stl, XY_Carriage.igs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]
2015-06-05 Added new models
    a) Panels for electronics enclosure
    b) Display / SD / Encoder enclosure
    [BackPanel1.igs, BackPanel1.stl, BackPanel2.igs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]
2015-06-05 Adjusted ports for EXP1 and EXP2
    (back of display enclosure)
    [Display3.igs, Display3.stl]
2015-06-05 Updated X end stop (Piggybacking on Y-Idler3)
    [Y-Idler3.igs, Y-Idler3.stl]
2015-06-07 Added Z idlers
    and Z stepper mount
    [Z-Axis-Guide-Top_1.igs, Z-Axis-Guide-Top_1.stl, Z-Axis-Guide-Top_2.igs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]
2015-06-08 Z-axis parts
    [Z-Axis-Guide-Bottom.igs, Z-Axis-Guide-Bottom.stl, Z-Axis-Guide-Middle.igs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]
2015-06-09 Resized stepper mounting holes
    [z-stepper-mount.igs, z-stepper-mount.stl]
2015-06-12 Added mounting bracket for Y rail
    [Rail_Bracket.igs, Rail_Bracket.stl]
2015-06-12 Updated Y idler3
    [Y-Idler3.igs, Y-Idler3.stl]
2015-06-13 Added impeller mount to hotend. Added z adjustment parts
    [Z-adjustment-block.igs, Z-adjustment-block.stl, Z-adjustment-dial.igs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]
2015-06-13 Updated z adjustment block
    [Z-adjustment-block.igs, Z-adjustment-dial.igs]
2015-06-14 Added fan duct. Removed generic E3D adapter
    [E3D_v6_New_Extruder.stp, extruder_air_duct.igs, extruder_air_duct.stl]
2015-06-15 Updated air duct
    [extruder_air_duct.igs, extruder_air_duct.stl]
2015-06-15 Added PCB Standoffs
    [PCB_Standoff.igs, PCB_Standoff.stl]
2015-06-16 Added Y towing mount
    [Y-Towing-Mount.igs, Y-Towing-Mount.stl]
2015-06-25 Dramatically simplified Z stabilizer / levelling
    It should now also be possible to support almost any type of Z-screw
    [Z-adjustment-1.igs, Z-adjustment-1.stl, Z-adjustment-2.igs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]
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2015-06-27 Updated brackets for Y towing chain
    [Y-Towing-Mount-2.igs, Y-Towing-Mount-2.stl, Y-Towing-Mount.igs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]
2015-06-27 Updated X towing chain support
    [X-Towing-Chain-Support.igs, X-Towing-Chain-Support.stl]
2015-06-28 Updated towing chain supports
    [X-Towing-Chain-Standoff.igs, X-Towing-Chain-Standoff.stl, X-Towing-Chain-Support-2.igs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]
2015-06-28 Added Z end stop
    [Z-Endstop-1.igs, Z-Endstop-1.stl, Z-Endstop-2.igs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]
2015-06-30 Updated Z endstops
    Also doubling as Y endstops
    [Z-Endstop-1.igs, Z-Endstop-1.stl, Z-Endstop-2.igs]
2015-07-18 Added cable clamps. Updated back panel
    [BackPanel1.igs, BackPanel1.stl, Cable_clamp.igs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]
2015-07-19 Updated config for 2mm pitch lead screw
    [Configuration.h]
2015-07-19 Added base plate shim
    To accomodate variations in base plate width
    [Z-Axis-Shim.igs, Z-Axis-Shim.stl]
2015-07-19 Added M8 version for Z screws
    [Z-adjustment-M8-1.igs, Z-adjustment-M8-1.stl, Z-adjustment-M8-2.igs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]
2015-07-19 Corrected this evening's brainfart
    [Z-adjustment-M8-1.igs, Z-adjustment-M8-1.stl, Z-adjustment-M8-2.igs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]
2015-07-20 Updated Z screws and config for M8. Updated belt clamps
    [Clamp1.igs, Clamp1.stl, Clamp2.igs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]
2015-07-21 Updated fan assembly
    [extruder_air_duct.igs, extruder_air_duct.stl]
2015-07-22 Updated belt clamps
    [Clamp1.igs, Clamp1.stl, Clamp2.igs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]
2015-07-22 Updated XY Idlers
    (They tended to flex in the Y direction)
    [XY_Idler_Left.igs, XY_Idler_Left.stl, XY_Idler_Right.igs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]
2015-08-01 Added bracket for geared z-stepper
    Also updated configuration.h with settings for geared stepper and 1/8
    microstepping for z-axis
    [Configuration.h, z-stepper-mount-geared.igs, z-stepper-mount-geared.stl]
2015-08-01 Fixed z drive shaft wobble
    (resulted in slight ribbing along the Z-axis. The problem is now totally
    annihilated :))
    [z-stepper-mount-geared.igs, z-stepper-mount-geared.stl]
2015-08-04 Updated firmware and Z-assembly
    [Configuration.h, Z-adjustment-1.igs, Z-adjustment-1.stl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]
2015-08-04 Updated steppermount
    [z-stepper-mount-geared.igs, z-stepper-mount-geared.stl]
2015-08-05 NAILED the problem regarding concentric z-ridges !
    Also updated firmware to give correct number of steps for T8 lead screw.
    [Configuration.h, z-stepper-mount-geared.igs, z-stepper-mount-geared.stl]

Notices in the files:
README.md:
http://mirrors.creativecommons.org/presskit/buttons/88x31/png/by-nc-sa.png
